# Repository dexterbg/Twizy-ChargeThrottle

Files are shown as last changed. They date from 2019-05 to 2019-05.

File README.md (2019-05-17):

# TwizyChargeThrottle

This is a very simple tool to limit the Twizy charge current if you don't have an OVMS.

It can limit the charge current to a fixed level (defined in the config file) or use a
coded rotary switch or simple DIP switch for dynamic level adjustment. It can signal
the charging state and active throttling by LEDs.

See [wiring scheme](extras/Wiring.pdf) for an example using a coded rotary switch.

The Arduino needs to be connected to the Twizy CAN bus during the charge process to be able
to actively overwrite the charge current control frames.

Note: using an interrupt capable CAN shield is highly recommended. No attempt at
reducing the Arduino current consumption is made, include a power switch or fork and
extend the code for sleep mode (and send me a pull request).

## Info

Author: Michael Balzer <dexter@dexters-web.de>

Libraries used:
  - MCP_CAN: https://github.com/coryjfowler/MCP_CAN_lib

This is free software under GNU Lesser General Public License (LGPL)
https://www.gnu.org/licenses/lgpl.html

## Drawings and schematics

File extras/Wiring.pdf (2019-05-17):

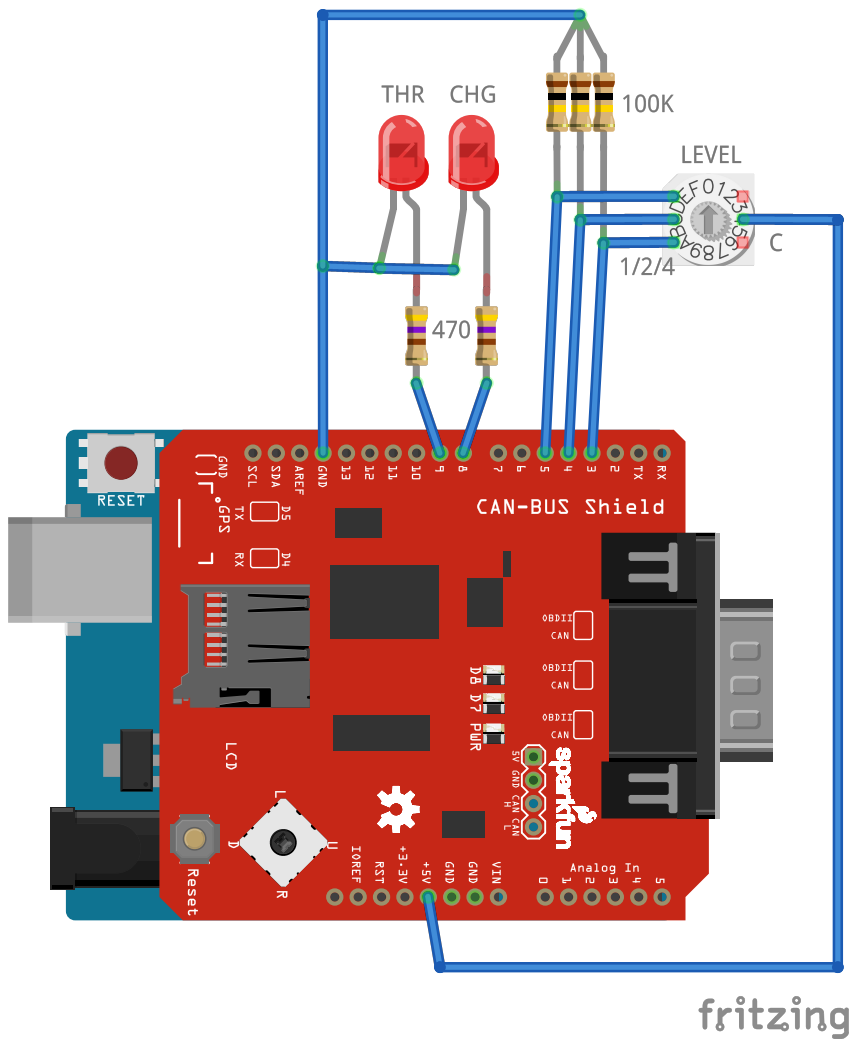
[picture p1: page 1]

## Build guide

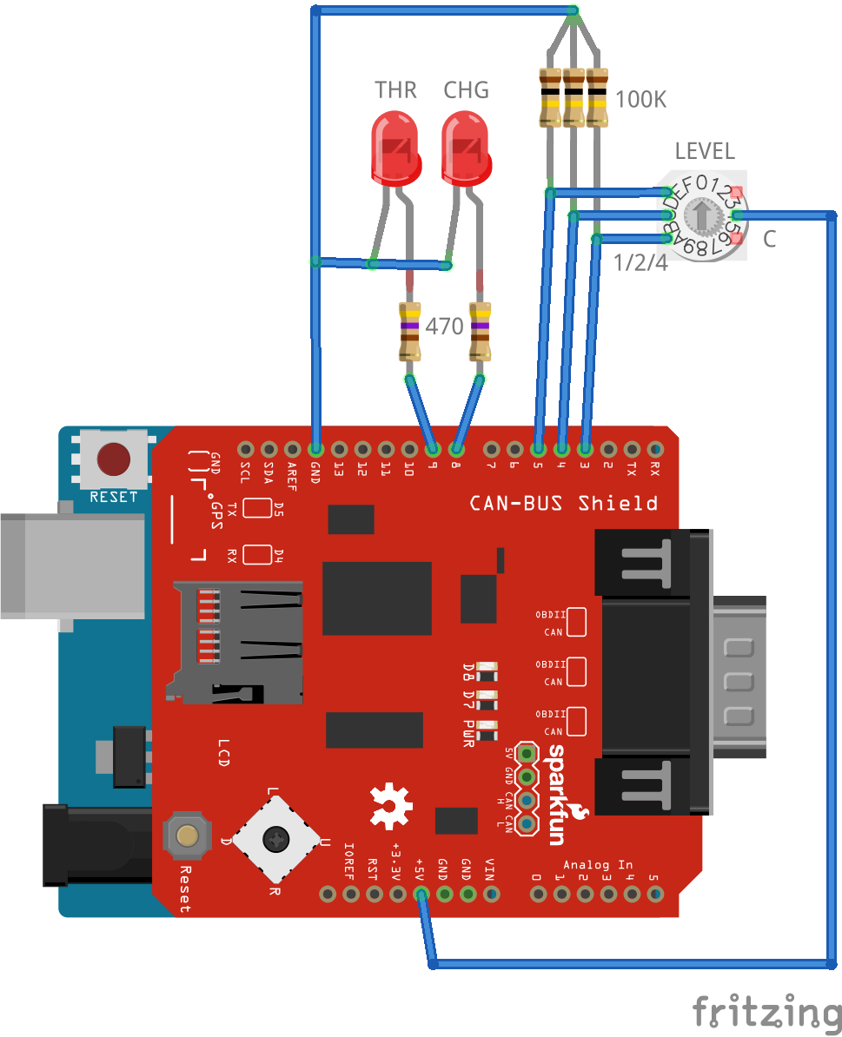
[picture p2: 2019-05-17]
extras/Wiring.png

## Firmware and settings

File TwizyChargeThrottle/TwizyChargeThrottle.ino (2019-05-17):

/**
 * ==========================================================================
 * Twizy charge current throttle
 * ==========================================================================
 * 
 * Author: Michael Balzer <dexter@dexters-web.de>
 * 
 * Libraries used:
 *  - MCP_CAN: https://github.com/coryjfowler/MCP_CAN_lib
 * 
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
 */
#define TWIZY_CT_VERSION "V2.0 (2019-05-17)"

#include <mcp_can.h>
#include <mcp_can_dfs.h>
#include "TwizyChargeThrottle_config.h"

#if TWIZY_DEBUG >= 1
  #define DEBUG1(cmd) cmd
#else
  #define DEBUG1(cmd)
#endif

// CAN interface:
MCP_CAN CAN(TWIZY_CAN_CS_PIN);

// CAN msg buffer:
unsigned long msgId;
byte msgLen;
byte msgBuf[8];

// Operation mode:
bool charging = false;

// Current level:
byte level = 0;

// Throttling level:
#ifdef FIXED_LEVEL
  const byte throttle = FIXED_LEVEL;
#else
  byte throttle = 0;
  #define READ_LEVEL() \
    ( digitalRead(IN_LEVEL_B1) \
    | digitalRead(IN_LEVEL_B2) << 1 \
    | digitalRead(IN_LEVEL_B4) << 2)
#endif


#if TWIZY_CAN_IRQ_PIN > 0
  volatile bool msgReceived = false;
  void canISR() {
    msgReceived = true;
  }
#endif


void setup() {
  
  Serial.begin(SERIAL_SPEED);
  Serial.println(F("TwizyChargeThrottle " TWIZY_CT_VERSION));
  
  // Init CAN interface:
  
  #if TWIZY_CAN_IRQ_PIN > 0
    pinMode(TWIZY_CAN_IRQ_PIN, INPUT);
    attachInterrupt(digitalPinToInterrupt(TWIZY_CAN_IRQ_PIN), canISR, FALLING);
  #endif

  while (CAN.begin(MCP_STDEXT, CAN_500KBPS, TWIZY_CAN_MCP_FREQ) != CAN_OK) {
    Serial.println(F("Setup: waiting for CAN connection..."));
    delay(1000);
  }
  
  // Set ID filters:
  
  CAN.init_Mask(0, 0, 0x07FF0000);
  CAN.init_Filt(0, 0, 0x01550000); // BMS → BMS: current control
  CAN.init_Filt(1, 0, 0x05970000); // CHG → BMS: operation mode
  
  CAN.init_Mask(1, 0, 0x07FF0000);
  CAN.init_Filt(2, 0, 0x00000000);
  CAN.init_Filt(3, 0, 0x00000000);
  CAN.init_Filt(4, 0, 0x00000000);
  CAN.init_Filt(5, 0, 0x00000000);
  
  CAN.setMode(MCP_NORMAL);

  // Init I/O:

  #ifndef FIXED_LEVEL
    pinMode(IN_LEVEL_B1, INPUT);
    pinMode(IN_LEVEL_B2, INPUT);
    pinMode(IN_LEVEL_B4, INPUT);
    throttle = READ_LEVEL();
  #endif

  pinMode(OUT_CHARGING_PIN, OUTPUT);
  pinMode(OUT_THROTTLING_PIN, OUTPUT);
  digitalWrite(OUT_CHARGING_PIN, LOW);
  digitalWrite(OUT_THROTTLING_PIN, LOW);

  Serial.println(F("Setup done."));

  Serial.print(F("Throttling to current level: "));
  Serial.println((char)('0' + throttle));
}


void loop() {
  while (true) {

    #if TWIZY_CAN_IRQ_PIN > 0
      // Wait for interrupt signal:
      while (!msgReceived);
      msgReceived = false;
    #endif

    // Process CAN read buffer:
    while (CAN.readMsgBuf(&msgId, &msgLen, msgBuf) == CAN_OK)
    {
      if (msgId == 0x597)
      {
        // ID 0x597: operation mode
        
        bool _charging = ((msgBuf[1] & 0x60) == 0x20);
        
        if (_charging && !charging)
        {
          digitalWrite(OUT_CHARGING_PIN, HIGH);
          #ifndef FIXED_LEVEL
            throttle = READ_LEVEL();
          #endif
          DEBUG1(Serial.println(F("Charge START")));
        }
        else if (!_charging && charging)
        {
          digitalWrite(OUT_CHARGING_PIN, LOW);
          digitalWrite(OUT_THROTTLING_PIN, LOW);
          DEBUG1(Serial.println(F("Charge STOP")));
        }
        
        charging = _charging;
        level = 0;
      }
      else if (charging)
      {
        // ID 0x155: charge current control

        byte _level = msgBuf[0];
        
        if (_level == 0xFF)
          continue; // init phase, skip
        
        if (throttle != 0 && _level > throttle)
        {
          // overwrite:
          msgBuf[0] = throttle;
          CAN.sendMsgBuf(0x155, 0, 8, msgBuf);
          digitalWrite(OUT_THROTTLING_PIN, HIGH);
        }
        else
        {
          digitalWrite(OUT_THROTTLING_PIN, LOW);
        }

        #if TWIZY_DEBUG > 1
          if (_level != level)
          {
            Serial.print(F("Level "));
            if (_level > throttle) {
              Serial.print((char)('0' + _level));
              Serial.print('>');
              Serial.println((char)('0' + throttle));
            } else {
              Serial.println((char)('0' + _level));
            }
          }
        #endif
        
        level = _level;
      }
    }

    #ifndef FIXED_LEVEL
      throttle = READ_LEVEL();
    #endif

  } // while (true)
}

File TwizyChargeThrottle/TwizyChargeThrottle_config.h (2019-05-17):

/**
 * ==========================================================================
 * Twizy charge current throttle
 * ==========================================================================
 */
#ifndef _TwizyChargeThrottle_config_h
#define _TwizyChargeThrottle_config_h

// Charge current throttle levels:
//  7 = 35 A = 2,3 kW (full power, no throttling)
//  6 = 30 A = 2,1 kW
//  5 = 25 A = 1,7 kW
//  4 = 20 A = 1,4 kW
//  3 = 15 A = 1,0 kW
//  2 = 10 A = 0,7 kW
//  1 =  5 A = 0,4 kW
//  0 = no throttling

// If not using a power level input, define a fixed throttling level like this:
// #define FIXED_LEVEL               5
// If this is defined, the power level inputs will not be used.

// Power level input:
// Use an 8 position binary coded rotary switch or a 3 pin DIP switch (or similar),
// define the input ports used here (analog ports may be used as well):
#define IN_LEVEL_B1               3
#define IN_LEVEL_B2               4
#define IN_LEVEL_B4               5

// Status outputs (e.g. LEDs):
#define OUT_CHARGING_PIN          8
#define OUT_THROTTLING_PIN        9

// Serial debug output level:
//  1 = show charge start/stop
//  2 = show current level changes
#define TWIZY_DEBUG               0

// Serial interface baud rate:
#define SERIAL_SPEED              115200

// Set your CAN MCP clock frequency here:
#define TWIZY_CAN_MCP_FREQ        MCP_16MHZ

// Set your CAN CS pin number here:
#define TWIZY_CAN_CS_PIN          10

// Set your CAN IRQ pin here (0 = no IRQ):
#define TWIZY_CAN_IRQ_PIN         2

#endif // _TwizyChargeThrottle_config_h

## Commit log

2019-05-15 Twizy-ChargeThrottle V1.0 (initial release)
2019-05-17 - Added support for level control input & state LEDs - Added example wiring scheme
    [Wiring.fzz]
